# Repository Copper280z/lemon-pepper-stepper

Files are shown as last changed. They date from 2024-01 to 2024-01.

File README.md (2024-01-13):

# Lemon Pepper Stepper Driver
Small, all in one hybrid stepper + BLDC driver, designed to mount to the back of NEMA 14/17 size stepper motors. The board supports up to 48V @ 1.5A with a choice of either step-dir, CAN bus, I2C, UART or USB input. Additionally, there are 5 GPIO broken out that can be used for a second encoder (AB hardware encoder or I2C), endstops or other general purposes. Current sensing is also included on-board.
The boards can easily be assembled by JLC and the design has been cost-optimized, coming in at about $20 per board fully assembled (minus connectors, which need to be modified to sit flat on motor back). 

Due to the high pole pair count of stepper motors, a high resolution (21 bit) magnetic encoder is used, supporting both SPI and hardware ABI position encoding. 
Despite the rather high theoretical performance of this board I think you would need some serious cooling to actually hit the potential 50-70W specs of the parts. A heatsink has been designed and produced that works well with the board, giving a uniform back profile and small fins for heat dissipation.
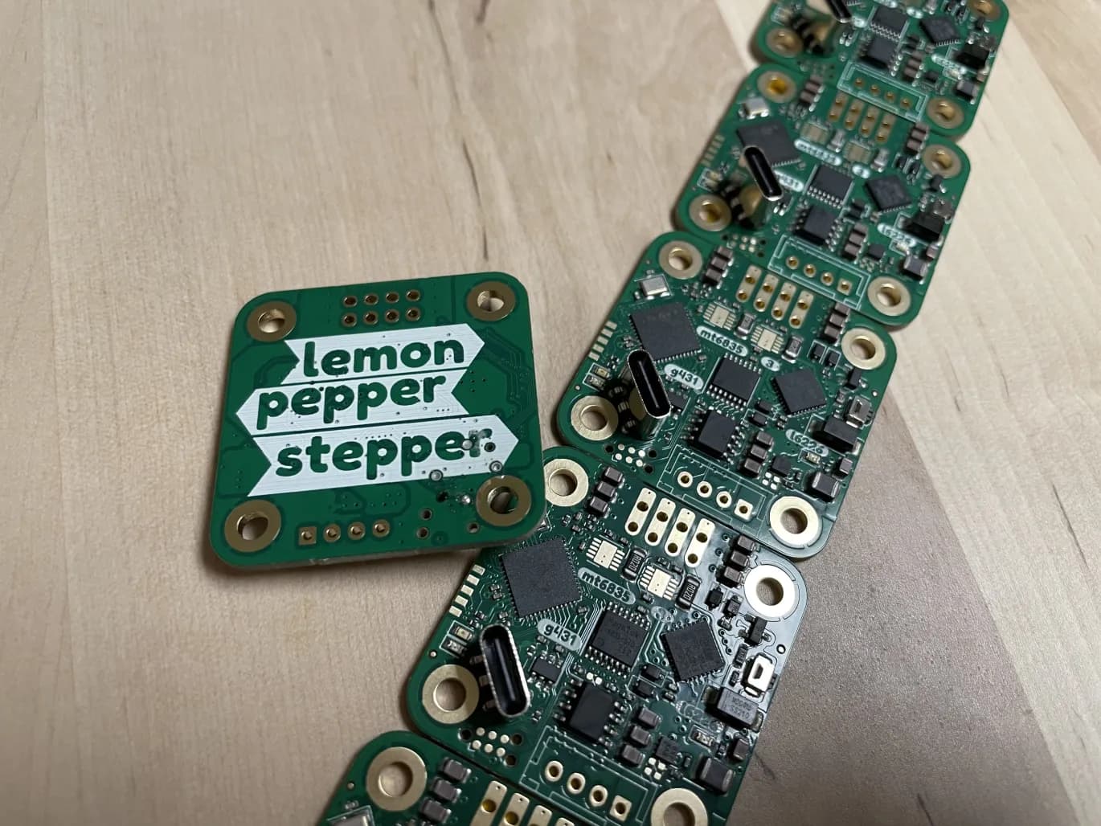
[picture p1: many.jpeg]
Photo of PCB

PCB on motor
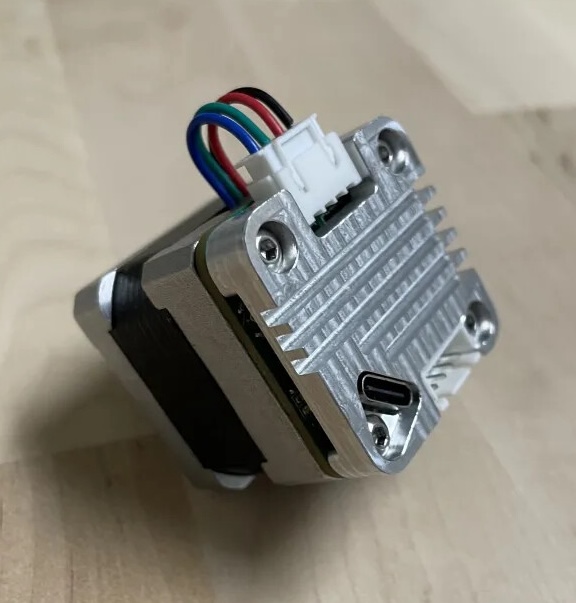
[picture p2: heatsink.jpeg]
Heatsink on motor


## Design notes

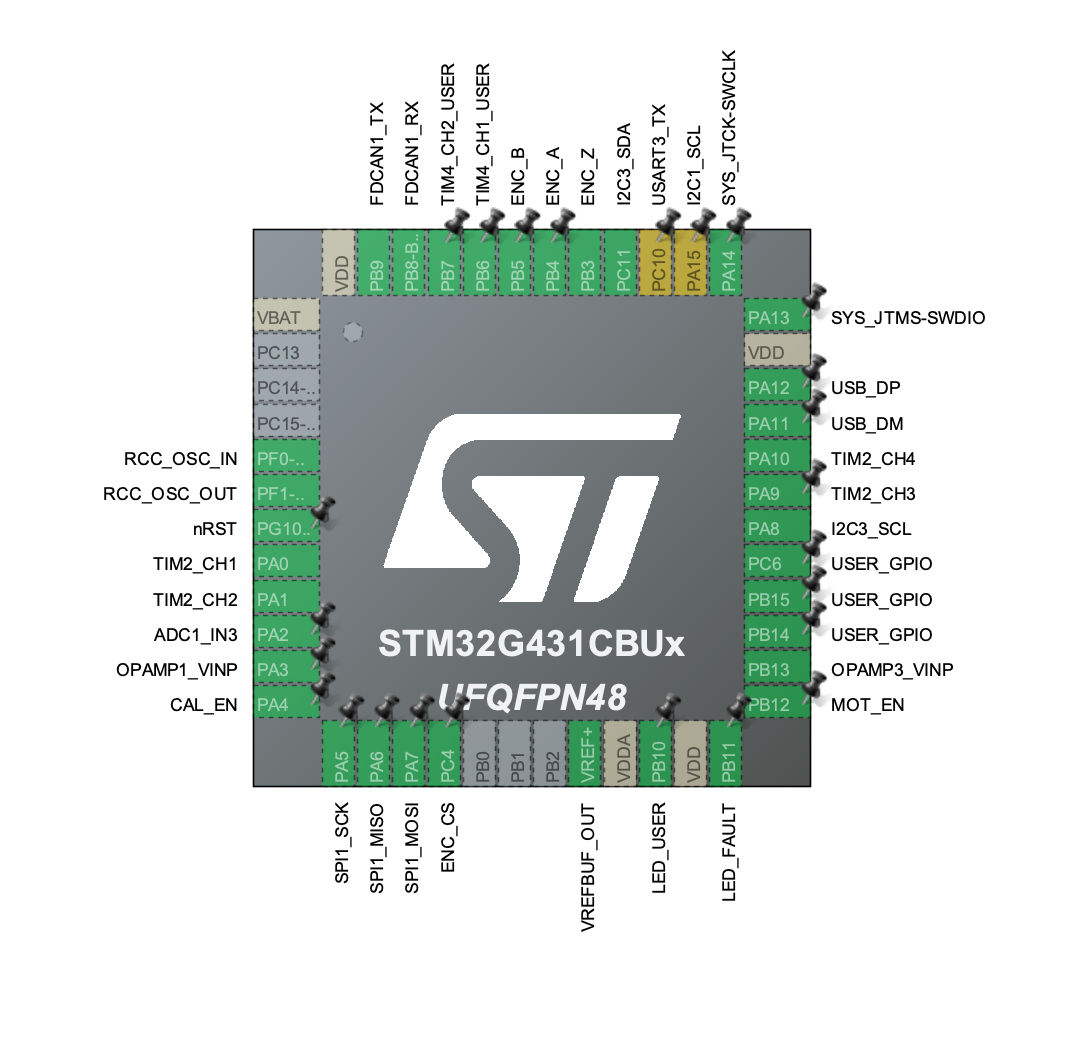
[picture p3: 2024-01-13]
pinout.png

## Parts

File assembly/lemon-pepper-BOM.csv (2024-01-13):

Comment | Designator | Footprint | JLCPCB Part #
10u | C101, C102, C103, C104, C105, C106, C107, C108, C501, C503 | 805 | C440198
47p | C201, C202 | 402 | C1567
1u | C301, C502 | 402 | C52923
100n | C302, C303, C304, C307, C308, C401, C701, C702, C703, C704 | 402 | C307331
20p | C305, C306 | 402 | C1554
10n | C601 | 402 | C15195
220n | C602 | 402 | C16772
SS210 | D101 | SMA | C14996
USER | D301 | 603 | C72041
FAULT | D302 | 603 | C2286
BZT52C30S | D501, D502 | SOD-323 | C22622
OCD | D601 | 603 | C2286
1N4148WS | D602, D603 | SOD-323 | C2128
USB_C_Receptacle_USB2.0 | J201 | USB C | C963223
33u | L501 | IND-SMD_L4.0-W4.0 | C602034
MMBT5551 | Q501 | SOT-23 | C2145
5k1 | R101, R102, R301, R302, R601 | 402 | C25905
120R | R103 | 402 | C25079
0R | R104, R105, R501, R702, R704 | 402 | C17168
51k | R303 | 402 | C25794
3k3 | R304 | 402 | C25890
10k | R305, R306, R401 | 402 | C25744
5R | R504 | 603 | C22936
15k | R505 | 402 | C25756
0R | R506 | 603 | C21189
20m | R701, R703 | 1206 | C393094
USER | SW301 | B3U-3000P | C963349
SRV05-4 | U201 | SOT-23-6 | C7420376
STM32G431 | U301 | QFN48 | C529356
SN65HVD230 | U302 | SOIC8 | C12084
MT6835 | U401 | TSSOP-16 | C2932578
MAX15062AATA+T | U501 | TDFN-8 | C2846801
L6226QTR | U601 | VQFN-32 | C95357
MAX49925 | U701, U703 | DFN-10 | C19193612
12MHz | Y301 | 3225 | C9002

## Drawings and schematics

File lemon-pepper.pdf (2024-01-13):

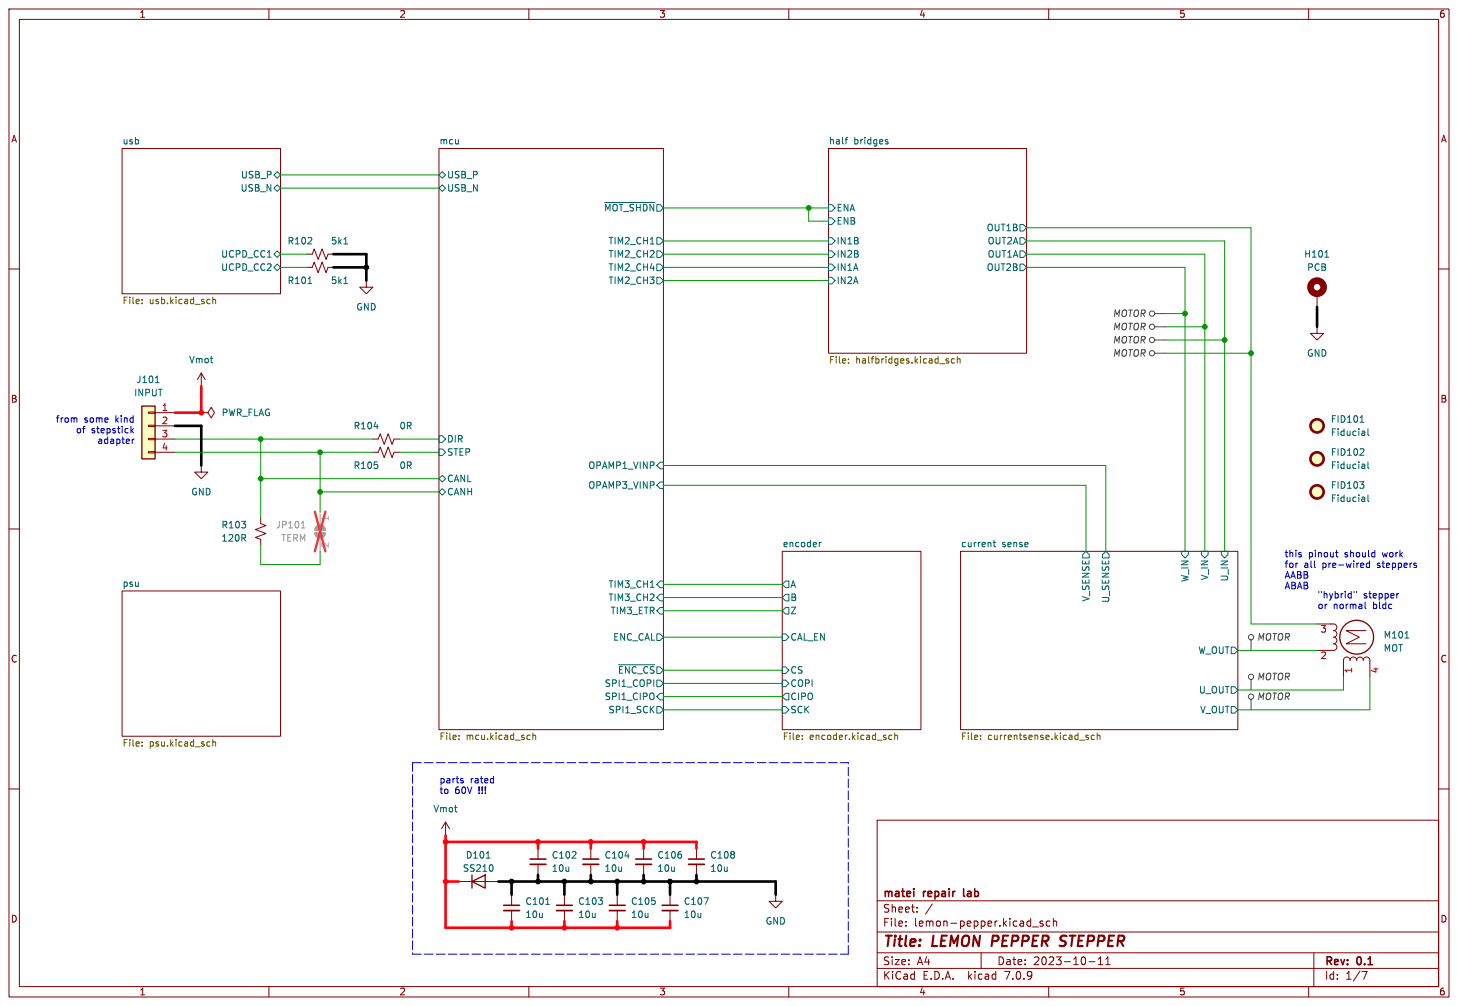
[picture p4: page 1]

4 M101 MOT Vmot GND GND

current sense File: currentsense.kicad_sch

this pinout should work

File: lemon-pepper.kicad_sch Sheet: / matei repair lab

Id: 1/7 Title: LEMON PEPPER STEPPER

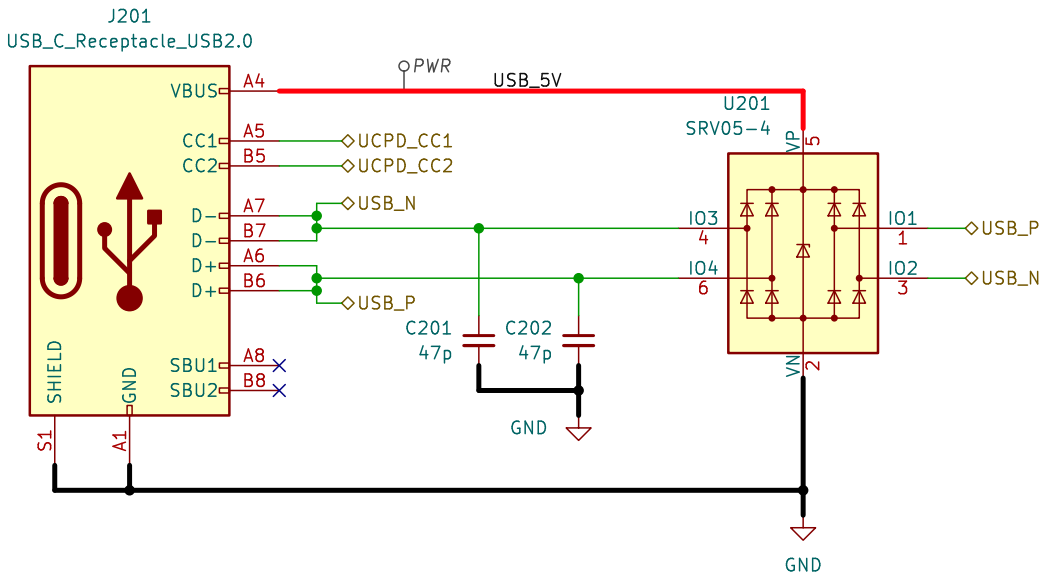
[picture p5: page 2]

File: usb.kicad_sch Sheet: /usb/ matei repair lab GND

Id: 2/7 Title: USB & ESD

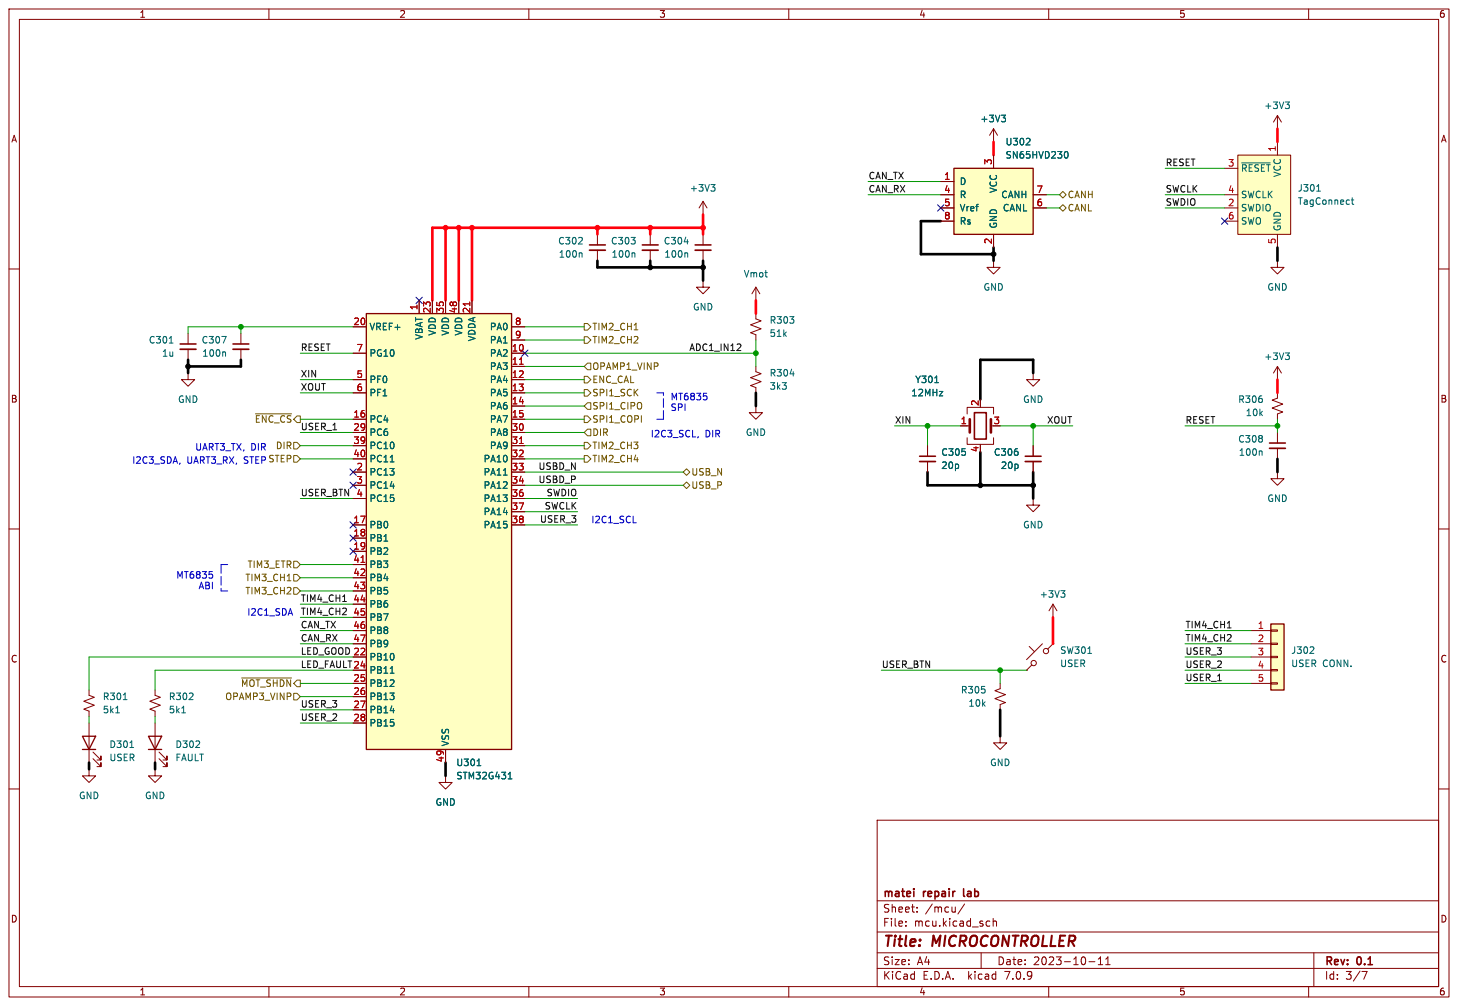
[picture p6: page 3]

1 SWDIO 2 ~{RESET} 3 SWCLK 4 GND

1 PA2 10 PA3 11 PA4 12 PA5 13 PA6 14 PA7 15 PC4 16 PB0 17 PB1 18 PB2 19 PC13 2 VREF+ 20 VDDA 21 PB10 22 VDD 23 PB11 24 PB12 25 PB13 26 PB14 27 PB15 28 PC6 29 PC14 3 PA8 30 PA9 31 PA10 32 PA11 33 PA12 34 VDD 35 PA13 36 PA14 37 PA15 38 PC10 39 PC15 4 PC11 40 PB3 41 PB4 42 PB5 43 PB6 44 PB7 45 PB8 46 PB9 47 VDD 48 VSS 49 PF0 5 PF1 6 PG10 7 PA0 8 PA1 9 U301 STM32G431 GND
TIM3_CH1 ~{MOT_SHDN} OPAMP3_VINP DIR
LED_FAULT USER_2 USER_BTN

1 PA2 10 PA3 11 PA4 12 PA5 13 PA6 14 PA7 15 PC4 16 PB0 17 PB1 18 PB2 19 PC13 2 VREF+ 20 VDDA 21 PB10 22 VDD 23 PB11 24 PB12 25 PB13 26 PB14 27 PB15 28 PC6 29 PC14 3 PA8 30 PA9 31 PA10 32 PA11 33 PA12 34 VDD 35 PA13 36 PA14 37 PA15 38 PC10 39 PC15 4 PC11 40 PB3 41 PB4 42 PB5 43 PB6 44 PB7 45 PB8 46 PB9 47 VDD 48 VSS 49 PF0 5 PF1 6 PG10 7 PA0 8 PA1 9 GND

File: mcu.kicad_sch Sheet: /mcu/ matei repair lab GND GND

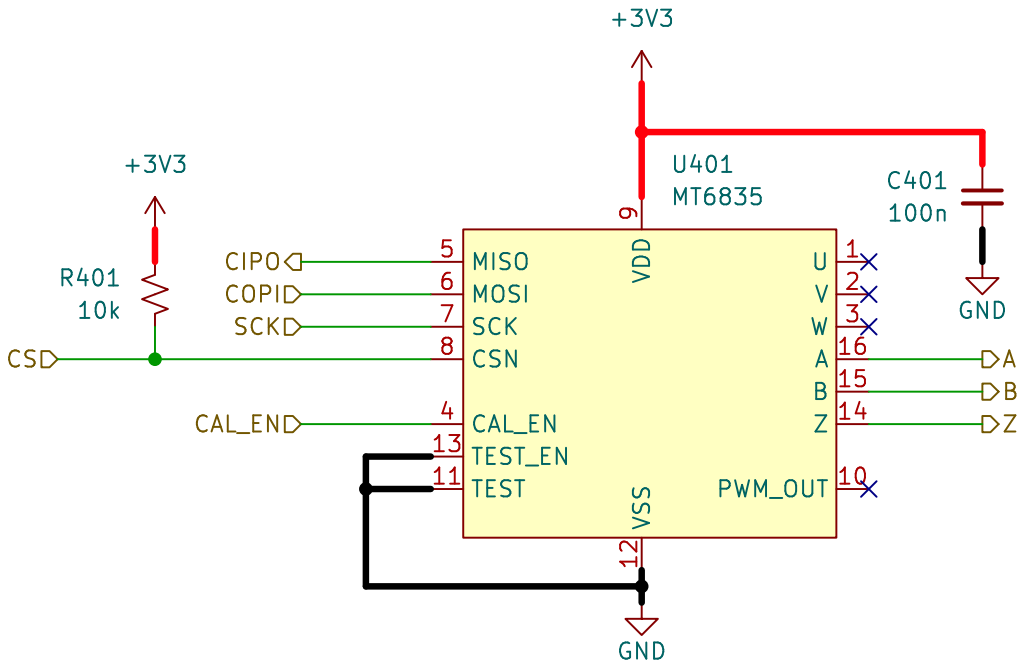
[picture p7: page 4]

File: encoder.kicad_sch Sheet: /encoder/ matei repair lab GND

Id: 4/7 Title: MAGNETIC ENCODER 14 BIT

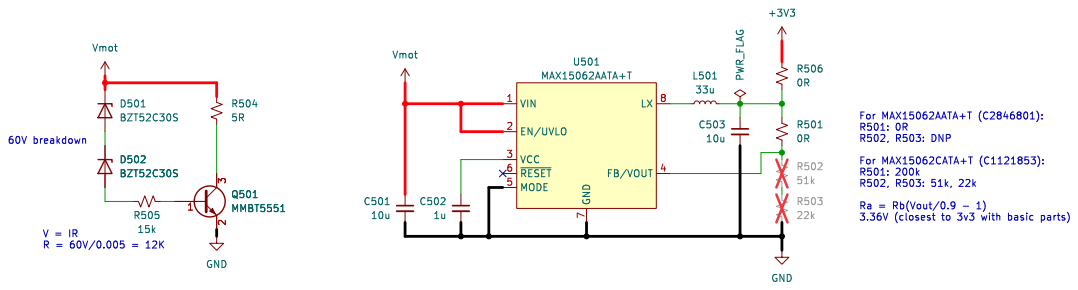
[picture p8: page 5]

File: psu.kicad_sch Sheet: /psu/ matei repair lab PWR_FLAG

Id: 6/7 Title: POWER SUPPLY & FILTERING

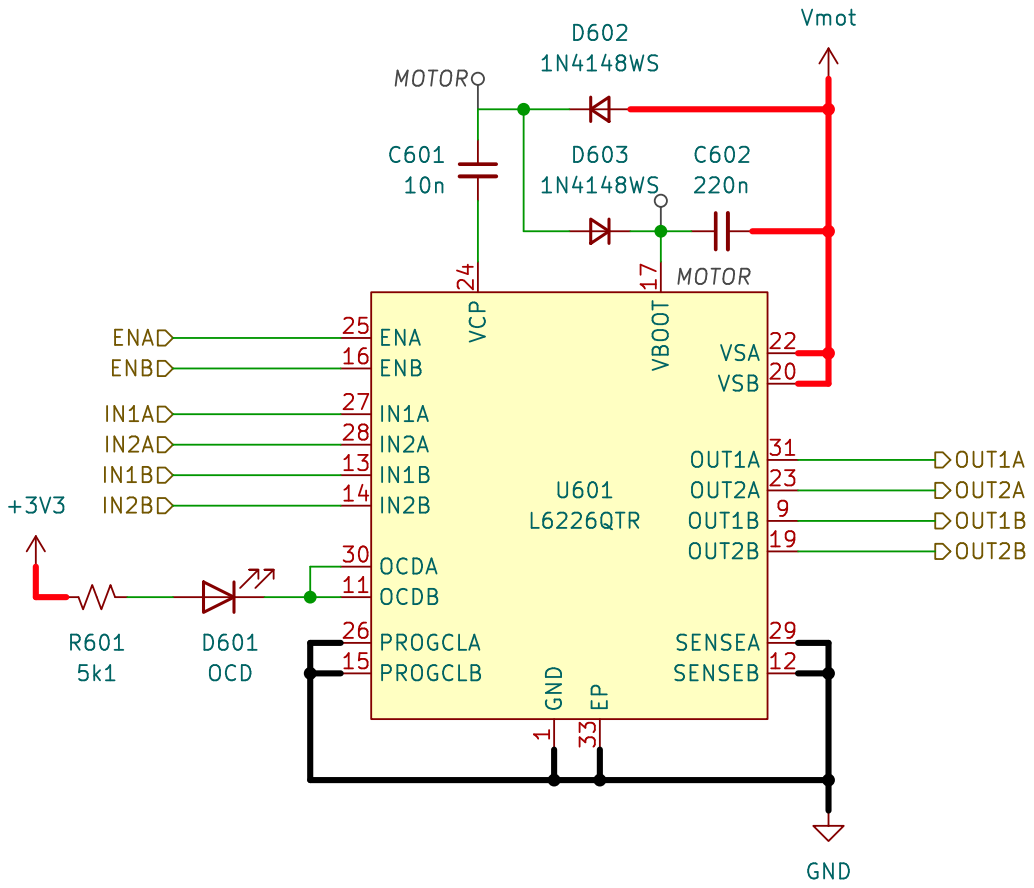
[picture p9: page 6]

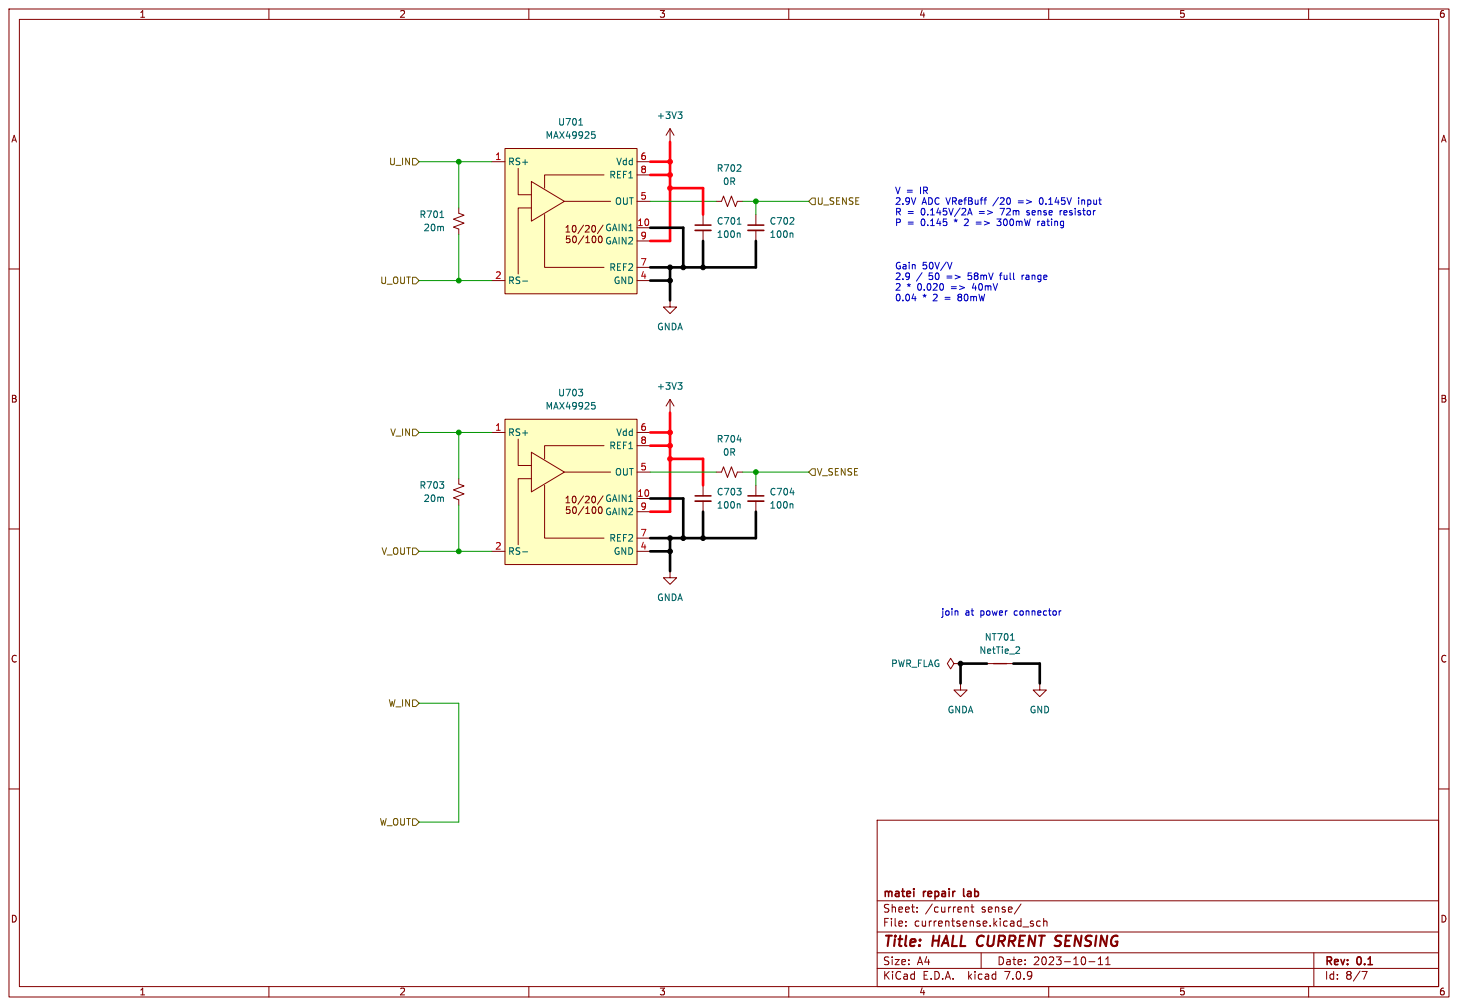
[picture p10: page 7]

join at power connector V = IR

Id: 8/7 Title: HALL CURRENT SENSING

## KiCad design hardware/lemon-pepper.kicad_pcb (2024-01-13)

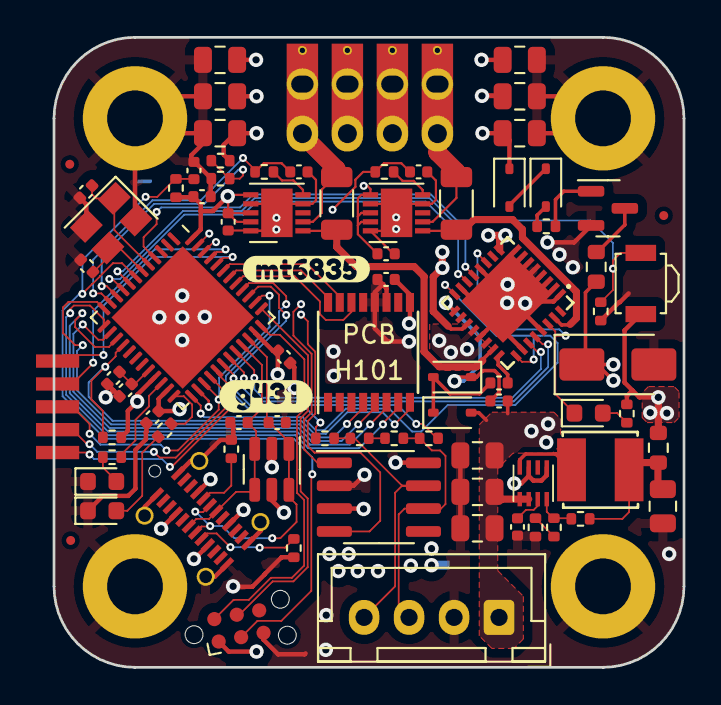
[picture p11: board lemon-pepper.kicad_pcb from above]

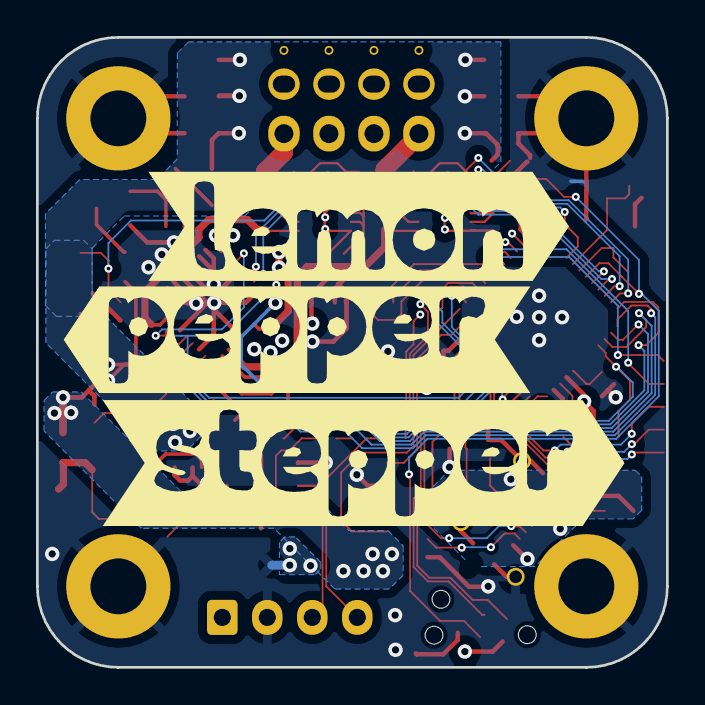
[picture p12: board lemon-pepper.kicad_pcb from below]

Board: 4 copper layers, 35.0 x 35.0 mm, 88 parts (4 on the bottom side), 70 nets.

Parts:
C101, C102, C103, C104, C105, C106, C107, C108, C501, C503: 10u; C_0805_2012Metric
C201, C202: 47p; C_0402_1005Metric
C301, C502: 1u; C_0402_1005Metric
C302, C303, C304, C307, C308, C401, C701, C702, C703, C704: 100n; C_0402_1005Metric
C305, C306: 20p; C_0402_1005Metric
C601: 10n; C_0402_1005Metric
C602: 220n; C_0402_1005Metric
D101: SS210; D_SMA
D301: USER; D_0603_1608Metric
D302: FAULT; D_0603_1608Metric
D501, D502: BZT52C30S; D_SOD-323
D601: OCD; D_0603_1608Metric
D602, D603: 1N4148WS; D_SOD-323
FID101, FID102, FID103: Fiducial; Fiducial_0.5mm_Mask1mm
H101: PCB; NEMA14
J101: INPUT; JST_XH_B4B-XH-A_1x04_P2.50mm_Vertical
J201: USB_C_Receptacle_USB2.0; usb_c
J301: TagConnect; Tag-Connect_TC2030-IDC-NL_2x03_P1.27mm_Vertical
J302: USER CONN.; PinHeader_1x05_P1.27mm_SMD
JP101: TERM; R_0402_1005Metric
L501: 33u; IND-SMD_L4.0-W4.0
M101: MOT; XH2.54 4P
NT701: NetTie_2; NetTie-2_SMD_Pad0.5mm
Q501: MMBT5551; SOT-23
R101, R102, R301, R302, R601: 5k1; R_0402_1005Metric
R103: 120R; R_0402_1005Metric
R104, R105, R501, R702, R704: 0R; R_0402_1005Metric
R303, R502: 51k; R_0402_1005Metric
R304: 3k3; R_0402_1005Metric
R305, R306, R401: 10k; R_0402_1005Metric
R503: 22k; R_0402_1005Metric
R504: 5R; R_0603_1608Metric
R505: 15k; R_0402_1005Metric
R506: 0R; R_0603_1608Metric
R701, R703: 20m; R_1206_3216Metric
SW301: USER; SW_SPST_B3U-3000P
U201: SRV05-4; SOT-23-6
U301: STM32G431; QFN-48-1EP_7x7mm_P0.5mm_EP5.6x5.6mm
U302: SN65HVD230; SOIC-8_3.9x4.9mm_P1.27mm
U401: MT6835; MagnTek TSSOP-16-1EP_4.4x5mm_P0.65mm
U501: MAX15062AATA+T; TDFN-8_L2.0-W2.0-P0.50-BL
U601: L6226QTR; ST-L6226Q-VQFN32
U701, U703: MAX49925; DFN-10-1EP_3x3mm_P0.5mm_EP1.75x2.7mm
Y301: 12MHz; Crystal_SMD_3225-4Pin_3.2x2.5mm
kibuzzard-65A1D30A: G***; kibuzzard-65A1D30A
kibuzzard-652C57F7: G***; kibuzzard-652C57F7
kibuzzard-652C580D: G***; kibuzzard-652C580D
kibuzzard-6557D15D: G***; kibuzzard-6557D15D
kibuzzard-6557D149: G***; kibuzzard-6557D149
kibuzzard-6557D153: G***; kibuzzard-6557D153

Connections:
+3V3: C302.1, C303.1, C304.1, C401.1, C701.1, C703.1, J301.1 (VCC), R306.1, R401.1, R506.1, R601.2, SW301.2, U301.21 (VDDA), U301.23 (VDD), U301.35 (VDD), U301.48 (VDD), U302.3 (VCC), U401.9 (VDD), U701.6 (Vdd), U701.8 (REF1), U701.9 (GAIN2), U703.6 (Vdd), U703.8 (REF1), U703.9 (GAIN2)
/current sense/U_IN: R701.1, U601.23 (OUT2A), U701.1 (RS+)
/current sense/U_OUT: M101.1, R701.2, U701.2 (RS-)
/current sense/U_SENSE: C702.1, R702.2, U301.11 (PA3)
/current sense/V_IN: R703.1, U601.31 (OUT1A), U703.1 (RS+)
/current sense/V_OUT: M101.4, R703.2, U703.2 (RS-)
/current sense/V_SENSE: C704.1, R704.2, U301.26 (PB13)
/current sense/W_IN: M101.2 (-), U601.19 (OUT2B)
/encoder/A: U301.42 (PB4), U401.16 (A)
/encoder/B: U301.43 (PB5), U401.15 (B)
/encoder/CAL_EN: U301.12 (PA4), U401.4 (CAL_EN)
/encoder/CIPO: U301.14 (PA6), U401.5 (MISO)
/encoder/COPI: U301.15 (PA7), U401.6 (MOSI)
/encoder/CS: R401.2, U301.16 (PC4), U401.8 (CSN)
/encoder/SCK: U301.13 (PA5), U401.7 (SCK)
/encoder/Z: U301.41 (PB3), U401.14 (Z)
/half bridges/ENA: U301.25 (PB12), U601.16 (ENB), U601.25 (ENA)
/half bridges/IN1A: U301.32 (PA10), U601.27 (IN1A)
/half bridges/IN1B: U301.8 (PA0), U601.13 (IN1B)
/half bridges/IN2A: U301.31 (PA9), U601.28 (IN2A)
/half bridges/IN2B: U301.9 (PA1), U601.14 (IN2B)
/half bridges/OUT1B: M101.3, U601.9 (OUT1B)
/mcu/ADC1_IN12: R303.2, R304.1, U301.10 (PA2)
/mcu/CANH: J101.4, JP101.1 (A), R105.2, U302.7 (CANH)
/mcu/CANL: J101.3, R103.1, R104.1, U302.6 (CANL)
/mcu/CAN_RX: U301.47 (PB9), U302.4 (R)
/mcu/CAN_TX: U301.46 (PB8), U302.1 (D)
/mcu/DIR: R104.2, U301.30 (PA8), U301.39 (PC10)
/mcu/LED_FAULT: R302.1, U301.24 (PB11)
/mcu/LED_GOOD: R301.1, U301.22 (PB10)
/mcu/RESET: C308.1, J301.3 (~RESET), R306.2, U301.7 (PG10)
/mcu/STEP: R105.1, U301.40 (PC11)
/mcu/SWCLK: J301.4 (SWCLK), U301.37 (PA14)
/mcu/SWDIO: J301.2 (SWDIO), U301.36 (PA13)
/mcu/TIM4_CH1: J302.1, U301.44 (PB6)
/mcu/TIM4_CH2: J302.2, U301.45 (PB7)
/mcu/USBD_N: C201.1, J201.A7 (D-), J201.B7 (D-), U201.3 (IO2), U201.4 (IO3), U301.33 (PA11)
/mcu/USBD_P: C202.1, J201.A6 (D+), J201.B6 (D+), U201.1 (IO1), U201.6 (IO4), U301.34 (PA12)
/mcu/USER_1: J302.5, U301.29 (PC6)
/mcu/USER_2: J302.4, U301.28 (PB15)
/mcu/USER_3: J302.3, U301.27 (PB14), U301.38 (PA15)
/mcu/USER_BTN: R305.1, SW301.1, U301.4 (PC15)
/mcu/XIN: C305.1, U301.5 (PF0), Y301.1
/mcu/XOUT: C306.1, U301.6 (PF1), Y301.3
/usb/UCPD_CC1: J201.A5 (CC1), R102.1
/usb/UCPD_CC2: J201.B5 (CC2), R101.2
/usb/USB_5V: J201.A4 (VBUS), J201.A9 (VBUS), J201.B4 (VBUS), J201.B9 (VBUS), U201.5 (VP)
GND: C101.1, C102.2, C103.1, C104.2, C105.1, C106.2, C107.1, C108.2, C201.2, C202.2, C301.2, C302.2, C303.2, C304.2, C305.2, C306.2, C307.2, C308.2, C401.2, C501.2, C502.2, C503.2, D101.2 (A), D301.1 (K), D302.1 (K), H101.1, J101.2, J201.A1 (GND), J201.A12 (GND), J201.B1 (GND), J201.B12 (GND), J201.S1 (SHIELD), J301.5 (GND), NT701.2, Q501.2 (E), R101.1, R102.2, R304.2, R305.2, R503.2, U201.2 (VN), U301.49 (VSS), U302.2 (GND), U302.8 (Rs), U401.11 (TEST), U401.12 (VSS), U401.13 (TEST_EN), U501.5 (MODE), U501.7 (GND), U601.1 (GND), U601.2 (NC), U601.3 (NC), U601.4 (NC), U601.5 (NC), U601.6 (NC), U601.7 (NC), U601.8 (NC), U601.12 (SENSEB), U601.15 (PROGCLB), U601.21 (GND), U601.26 (PROGCLA), U601.29 (SENSEA), U601.33 (EP), Y301.2, Y301.4
GNDA: C701.2, C702.2, C703.2, C704.2, NT701.1, U701.4 (GND), U701.7 (REF2), U701.10 (GAIN1), U701.11 (EP), U703.4 (GND), U703.7 (REF2), U703.10 (GAIN1), U703.11 (EP)
unnamed: C503.1, L501.2, R501.1, R506.2
unnamed: D301.2 (A), R301.2
unnamed: D302.2 (A), R302.2
unnamed: D501.2 (A), D502.1 (K)
unnamed: D502.2 (A), R505.1
unnamed: D601.2 (A), R601.1
unnamed: D601.1 (K), U601.11 (OCDB), U601.30 (OCDA)
unnamed: C601.1, D602.1 (K), D603.2 (A)
unnamed: C602.1, D603.1 (K), U601.17 (VBOOT)
unnamed: JP101.2 (B), R103.2
unnamed: Q501.1 (B), R505.2
unnamed: Q501.3 (C), R504.2
unnamed: R502.2, R503.1
unnamed: C301.1, C307.1, U301.20 (VREF+)
unnamed: R501.2, R502.1, U501.4 (FB/VOUT)
unnamed: L501.1, U501.8 (LX)
unnamed: C502.1, U501.3 (VCC)
unnamed: C601.2, U601.24 (VCP)
unnamed: R702.1, U701.5 (OUT)
unnamed: R704.1, U703.5 (OUT)
Vmot: C101.2, C102.1, C103.2, C104.1, C105.2, C106.1, C107.2, C108.1, C501.1, C602.2, D101.1 (K), D501.1 (K), D602.2 (A), J101.1, R303.1, R504.1, U501.1 (VIN), U501.2 (EN/UVLO), U601.20 (VSB), U601.22 (VSA)

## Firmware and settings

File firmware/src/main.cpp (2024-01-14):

#include <Arduino.h>
#include <EEPROM.h>
#include <SPI.h>

#include "SimpleFOC.h"
#include "SimpleFOCDrivers.h"
#include "encoders/mt6835/MagneticSensorMT6835.h"
#include "encoders/stm32hwencoder/STM32HWEncoder.h"
#include "utilities/stm32math/STM32G4CORDICTrigFunctions.h"

#include "stm32g4xx_hal_conf.h"
#include "stm32g4xx_hal_fdcan.h"

#include "can.h"
#include "dfu.h"
#include "utils.h"
#include "InlineCurrentSenseSync.h"
#include "lemon-pepper.h"
#include "old.h"
#include "sfoc_tools.h"


#define USBD_MANUFACTURER_STRING "matei repair lab"
#define USBD_PRODUCT_STRING_FS "lemon-pepper-stepper"

// board specific data
typedef struct
{
	uint16_t signature;
	Direction electricalDir;
	float electricalZero;
	uint16_t abzResolution;
	uint8_t encoderCalibrated;
	uint8_t canID;
} userData;

userData boardData;
uint8_t updateData = 0;

const uint16_t magicWord = 0xAF0C;

// canbus things
extern volatile uint8_t TxData[8];
extern volatile uint8_t RxData[8];

// simpleFOC things
#define POLEPAIRS 50
#define RPHASE 2.0
#define MOTORKV 40
#define ENC_PPR 16383 // max 16383 (zero index) -> *4 for CPR, -1 is done in init to prevent rollover on 16 bit timer

#define SERIALPORT SerialUSB

// HardwareSerial Serial3 = HardwareSerial(PB8, PB9);

/**
 * SPI clockdiv of 16 gives ~10.5MHz clock. May still be stable with lower divisor.
 * The HW encoder is configured using PPR, which is then *4 for CPR (full 12384 gives overflow on 16 bit timer.)
 */
SPISettings myMT6835SPISettings(168000000 / 10, MT6835_BITORDER, SPI_MODE3);
MagneticSensorMT6835 sensor = MagneticSensorMT6835(ENC_CS, myMT6835SPISettings);
// SPISettings myMT6835SPISettings(168000000 / 10, MT6835_BITORDER, SPI_MODE3);
// MagneticSensorMT6835 sensor = MagneticSensorMT6835(ENC_CS);
STM32HWEncoder enc = STM32HWEncoder(ENC_PPR, ENC_A, ENC_B, ENC_Z);

/**
 * TODO: Change the current sense code to reflect the new inline current sense amplifier choice with sense resistor.
 */
// InlineCurrentSenseSync currentsense = InlineCurrentSenseSync(90, ISENSE_U, ISENSE_V, ISENSE_W);


StepperDriver4PWM driver = StepperDriver4PWM(PA0, PA9, PA1, PA10, PB12);
StepperMotor motor = StepperMotor(POLEPAIRS, RPHASE, MOTORKV, 0.0035);
StepDirListener step_dir = StepDirListener( PC11, PA8, _2PI/(200.0*16) );
void onStep() { step_dir.handle(); }

int time_prev;


SineSweep sine_test = SineSweep();
PRBS prbs_test = PRBS();

Commander commander = Commander(SERIALPORT);

uint16_t counter = 0;
float stepCounter;

DQCurrent_s foc_currents;
float electrical_angle;
PhaseCurrent_s phase_currents;

// Prototypes
uint8_t configureFOC(void);
uint8_t configureCAN(void);
void calibrateEncoder(char *c);
void userButton(void);
void onStep(void) {step_dir.handle();}

void sineExecute(char* c) {
	sine_test.Execute();
}

void prbsExecute(char* c) {
	prbs_test.Execute_args(c);
}

void setup()
{
	sine_test.amplitude = 0.1;
	pinMode(LED_GOOD, OUTPUT);
	pinMode(LED_FAULT, OUTPUT);
	pinMode(CAL_EN, OUTPUT);
	pinMode(MOT_EN, OUTPUT);
	// pinMode(USER_BUTTON, INPUT);
    SimpleFOC_CORDIC_Config();      // initialize the CORDIC

	// attachInterrupt(USER_BUTTON, userButton, RISING);


	SERIALPORT.begin(2000000);

	EEPROM.get(0, boardData);

	digitalWrite(MOT_EN, HIGH);
	digitalWrite(CAL_EN, LOW);

	uint8_t ret;
	// ret = configureCAN();
	// if (!ret){
	// 	SIMPLEFOC_DEBUG("CAN init failed.");
	// 	digitalWrite(LED_FAULT, HIGH);
	// }


	step_dir.init();
	step_dir.enableInterrupt(onStep);
    step_dir.attach(&motor.target, &motor.feed_forward_velocity);

	ret = configureFOC();
	if (!ret){
		SIMPLEFOC_DEBUG("FOC init failed.");
		digitalWrite(LED_FAULT, HIGH);
	}

	if (sensor.getABZResolution() != ENC_PPR) // Check that PPR of the encoder matches our expectation.
	{
		digitalWrite(LED_FAULT, HIGH);
		SIMPLEFOC_DEBUG("Encoder ABZ resolution unexpected.");
	}


	time_prev=micros();

	sine_test.linkMotor(&motor);
	sine_test.linkSerial(&SERIALPORT);
	
	prbs_test.linkMotor(&motor);
	prbs_test.linkSerial(&SERIALPORT);
	
	// commander.scalar(&test.max_frequency, (char*)'x');
	// commander.scalar(&test.min_frequency, (char*)'n');
	// commander.scalar(&test.amplitude, (char*)'a');
	// commander.scalar(&test.steps, (char*)'s');
	// commander.scalar(&test.cycles_per_step, (char*)'c');

	commander.add('X', &sineExecute);
	commander.add('P', &prbsExecute);
	commander.add('E', &calibrateEncoder);

	SERIALPORT.println("BMP Over TCP!!!");


}


void loop()
{

	step_dir.cleanLowVelocity();  
	motor.move();
	motor.loopFOC();
	commander.run();


	if(counter == 0xFFFF){
		digitalToggle(LED_GOOD);
		counter = 0;
	}

	counter++;

#ifdef HAS_MONITOR
	motor.monitor();
#endif
}

void doMotor(char *cmd)
{
	commander.motor(&motor, cmd);
}

uint8_t configureFOC(void)
{
	commander.add('M', doMotor, "motor");
	commander.verbose = VerboseMode::machine_readable;

#ifdef SIMPLEFOC_STM32_DEBUG
	SimpleFOCDebug::enable(&SERIALPORT);
#endif

	// Encoder initialization.
	// Ideally configuring the sensor over SPI then use STM32HWEncoder

	step_dir.init();
	step_dir.enableInterrupt(onStep);
	step_dir.attach(&stepCounter);

	enc.init();
	if (!enc.initialized)
		digitalWrite(LED_FAULT, HIGH);

	sensor.init();
	// sensor.setHysteresis(7);
	// Check if the encoder has loaded the right PPR, if not, update and then write to EEPROM.
	if (sensor.getABZResolution() != ENC_PPR)
	{
		delay(200);
		sensor.setABZResolution(ENC_PPR);
		sensor.writeEEPROM();

		digitalWrite(LED_GOOD, HIGH);
		digitalWrite(LED_FAULT, LOW);

		for (uint8_t i = 0; i < 60; i++)
		{ // Datasheet says we need to wait 6 seconds after writing EEPROM.
			digitalToggle(LED_GOOD);
			digitalToggle(LED_FAULT);
			delay(100);
		}

		digitalWrite(LED_GOOD, LOW);
		digitalWrite(LED_FAULT, LOW);
	}

	// Driver initialization.
	driver.pwm_frequency = 35000;
	driver.voltage_power_supply = 12.0f;
	driver.voltage_limit = driver.voltage_power_supply/2.0f;
	driver.init();

	// Motor PID parameters.
    motor.PID_velocity.P = 0.075f;
    motor.PID_velocity.I = 4.0f;
    motor.PID_velocity.D = 0.00f;
    motor.LPF_velocity.Tf = 0.0015f;
	motor.PID_velocity.output_ramp = 0.0f;
	motor.PID_velocity.limit = 500.0f;

	motor.P_angle.P = 400.0f;
    motor.P_angle.I = 5.0f;
    motor.P_angle.D = 1.0f;
	motor.LPF_angle.Tf = 0.00f; // try to avoid

	motor.motion_downsample = 1;

	// Motor initialization.
	motor.voltage_sensor_align = 2.0f;
	motor.current_limit = 2.0f;
	motor.velocity_limit = 500;
	motor.controller = MotionControlType::angle;
	motor.foc_modulation = FOCModulationType::SpaceVectorPWM;

// Monitor initialization
#ifdef HAS_MONITOR
	motor.useMonitoring(SERIALPORT);
	motor.monitor_start_char = 'M';
	motor.monitor_end_char = 'M';
	motor.monitor_downsample = 250;
#endif

	motor.linkSensor(&sensor);
	motor.linkDriver(&driver);

	// currentsense.linkDriver(&driver);
	// int ret = currentsense.init();
	// SERIALPORT.printf("Current Sense init result: %i\n", ret);
	// motor.linkCurrentSense(&currentsense);



	// motor.zero_electric_angle = 0.24; // small motor
	motor.zero_electric_angle = 0.625; // big motor
	motor.sensor_direction = Direction::CCW;

	motor.init();
	motor.initFOC();


	// calibrateEncoder();
	sensor.update();
	float start_angle = motor.shaftAngle();
	SERIALPORT.printf("Setting target to: %.2f\n", start_angle);
	motor.target = start_angle;
	// if(boardData.signature != magicWord){
	// 	// If we have not initialized the EEPROM before.
	// 	motor.init();
	// 	motor.initFOC();

	// 	boardData.signature = magicWord;
	// 	boardData.electricalZero = motor.zero_electric_angle;
	// 	boardData.electricalDir = motor.sensor_direction;
	//  updateData = 1;
	// }
	// else{
	// 	motor.zero_electric_angle = boardData.electricalZero;
	// 	motor.sensor_direction = boardData.electricalDir;
	// 	motor.init();
	// 	motor.initFOC();
	// }

	return 1;
}

uint8_t configureCAN(void)
{
	FDCAN_Start(0x000);
	return 1;
}

void calibrateEncoder(char* c)
{
	MotionControlType orig_controller = motor.controller;
	motor.controller = MotionControlType::velocity_openloop;
	motor.enable();

	motor.target = 7; // roughly 150rpm -> need to write 0x5 to Reg. AUTOCAL_FREQ
	int revs = 64;
	MT6835Options4 currentSettings = sensor.getOptions4();
	currentSettings.autocal_freq = 0x6;
	sensor.setOptions4(currentSettings);

	uint32_t calTime = micros();
	while ((micros() - calTime) < ((revs/(motor.target/_2PI) + 1.2)*1e6))
	{
		motor.loopFOC();
		motor.move();

		if ((micros() -calTime) > 200000)
		{
			// after motor is spinning at constant speed, enable calibration.
			digitalWrite(LED_GOOD, HIGH);
			digitalWrite(CAL_EN, HIGH);
		}
	}
	motor.target = 0;
	digitalWrite(LED_GOOD, LOW);
	digitalWrite(CAL_EN, LOW);
	motor.controller = orig_controller;

	digitalWrite(LED_GOOD, HIGH);
	digitalWrite(LED_FAULT, LOW);

	for (uint8_t i = 0; i < 60; i++)
	{ // Datasheet says we need to wait 6 seconds after writing EEPROM.
		digitalToggle(LED_GOOD);
		digitalToggle(LED_FAULT);
		delay(100);
	}

	digitalWrite(LED_GOOD, LOW);
	digitalWrite(LED_FAULT, LOW);

	// return sensor.getCalibrationStatus();
	return;
}

void userButton(void)
{
	if(USB->DADDR != 0)
		jump_to_bootloader();
	else
		digitalToggle(LED_FAULT);
}

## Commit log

2024-01-03 Starting printer config, including makefile and compile_commands.json for vim pio
2024-01-05 config PIO to use a remote black magic debug probe to upload firmware
